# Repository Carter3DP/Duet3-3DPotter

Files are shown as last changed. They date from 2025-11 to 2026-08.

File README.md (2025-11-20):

# Duet3-Mainboard-3DP

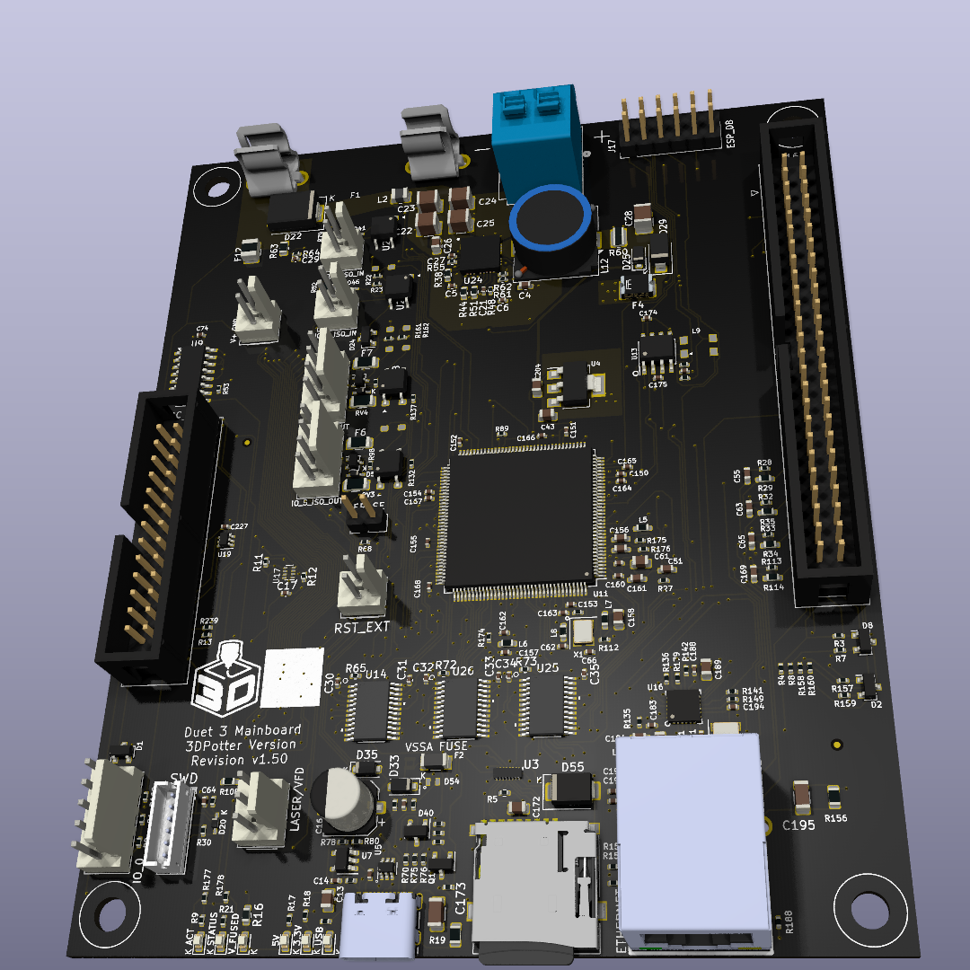
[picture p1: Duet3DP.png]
Render of the board.


This board is a fork of the Duet3 6XD with a little of the 6HC. You can find
them here:

[https://github.com/Duet3D/Duet3-Mainboard-6XD](https://github.com/Duet3D/Duet3-Mainboard-6XD)

[https://github.com/Duet3D/Duet3-Mainboard-6HC](https://github.com/Duet3D/Duet3-Mainboard-6HC)

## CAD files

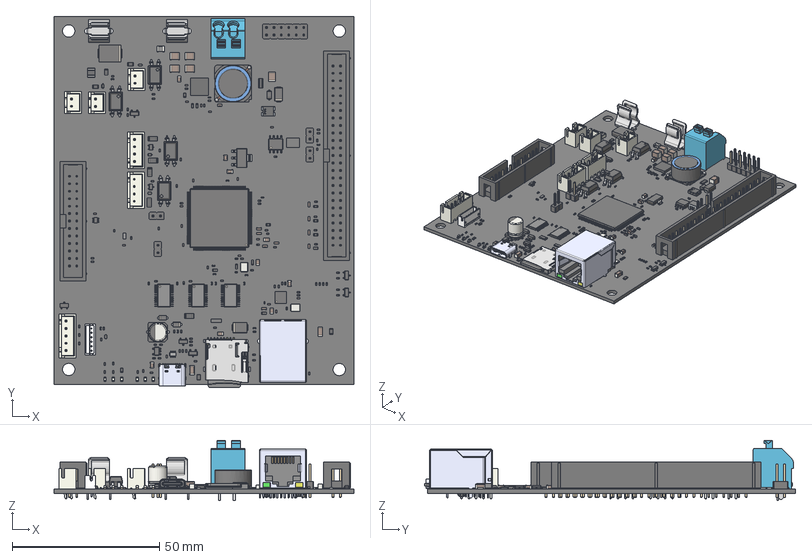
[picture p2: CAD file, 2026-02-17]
CAD/Duet3_MB_3DP.step
101.9 x 126.2 x 20.5 mm
R_0402_1005Metric x 77
SOT-23 x 6
Crystal_SMD_3225-4Pin_3.2x2.5mm x 2
C_0603_1608Metric x 10
BxB-ZR_6
pin_straight x 4
pin_Bent x 2
LED_0603_1608Metric x 6
LQFP-144_20x20mm_P0.5mm
R_0805_2012Metric x 5
R_0603_1608Metric x 13
L_Wurth_WE-CNSW-1812
PinHeader_1x02_P2.54mm_Vertical x 4
D_SOD-523 x 5
C_1206_3216Metric x 2
C_0402_1005Metric x 45
C_0805_2012Metric x 9
SOT-223
Fuse_1206_3216Metric x 3
IDC-Header_2x13_P2.54mm_Vertical
JST_XH_B2B-XH-A_1x02_P2.50mm_Vertical x 3
QFN-24-1EP_4x4mm_P0.5mm_EP2.6x2.6mm
SOIC-8_3.9x4.9mm_P1.27mm
HR911105A_HR911105A
Case^MicroSD_Socket
Insert^MicroSD_Socket
Brace^MicroSD_Socket
Spring^MicroSD_Socket
Lid^MicroSD_Socket
Pin_Middle^MicroSD_Socket x 5
Pin_Short^MicroSD_Socket
Pin_Long^MicroSD_Socket x 2
MicroSD_Card^MicroSD_Socket
Pin_CardIn^MicroSD_Socket
JST_XH_B5B-XH-A_1x05_P2.50mm_Vertical
D_SMB
Fuse_1210_3225Metric
JST_XH_B4B-XH-A_1x04_P2.50mm_Vertical x 2
Pin x 8
SOT-323_SC-70 x 2
R_1206_3216Metric x 2
USB4105GFA_USB4105GFA
L_TDK_SLF12575
PinsArrayLR
CP_Elec_6.3x7.7
PinHeader_2x06_P2.54mm_Vertical
C_1210_3225Metric x 5
BODY-TSSOP x 3
LEAD-TSSOP x 72
PIN1 x 3
R_0612_1632Metric
D_SOD-123F x 3
L_1008_2520Metric
D_SMC
IDC-Header_2x25_P2.54mm_Vertical
D_SMA
MICROQFN16_1P25X3P55X0P4_STM
SOT-23-5
SC70_RCLAMP_SEM
Intersect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

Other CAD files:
CAD/Duet3_MB_6XD.step
CAD/Duet3_MB_3DP (2).step

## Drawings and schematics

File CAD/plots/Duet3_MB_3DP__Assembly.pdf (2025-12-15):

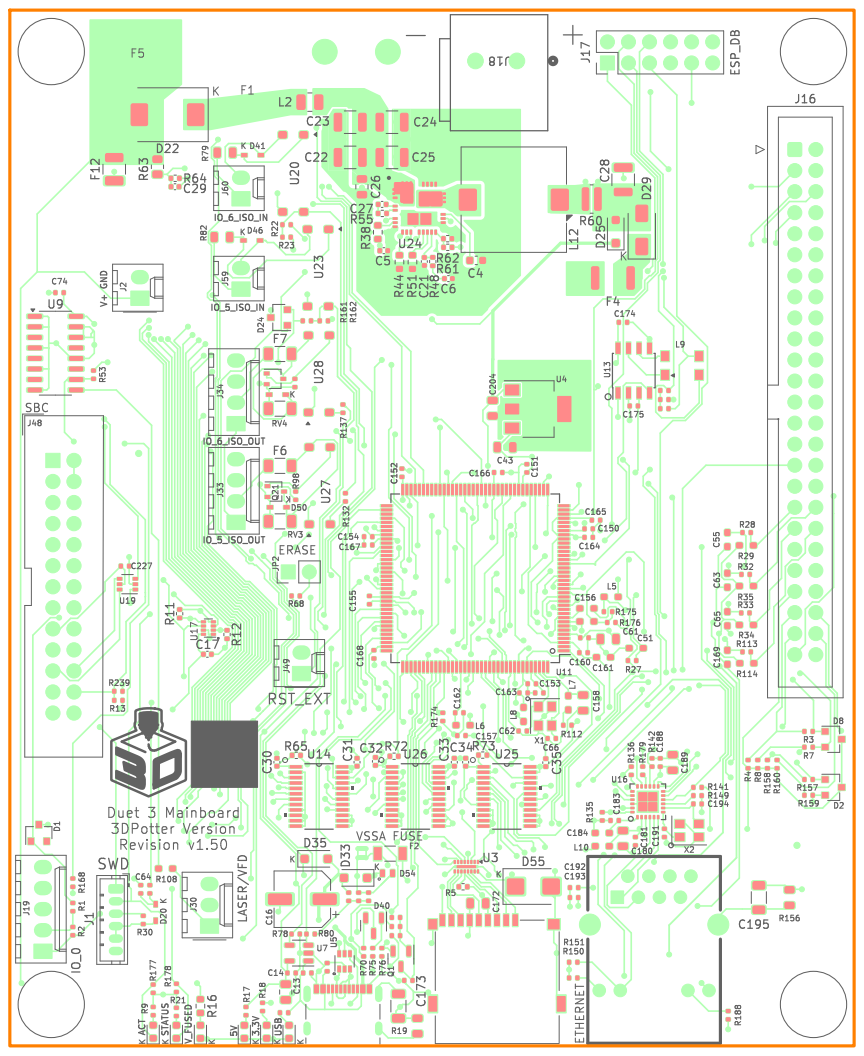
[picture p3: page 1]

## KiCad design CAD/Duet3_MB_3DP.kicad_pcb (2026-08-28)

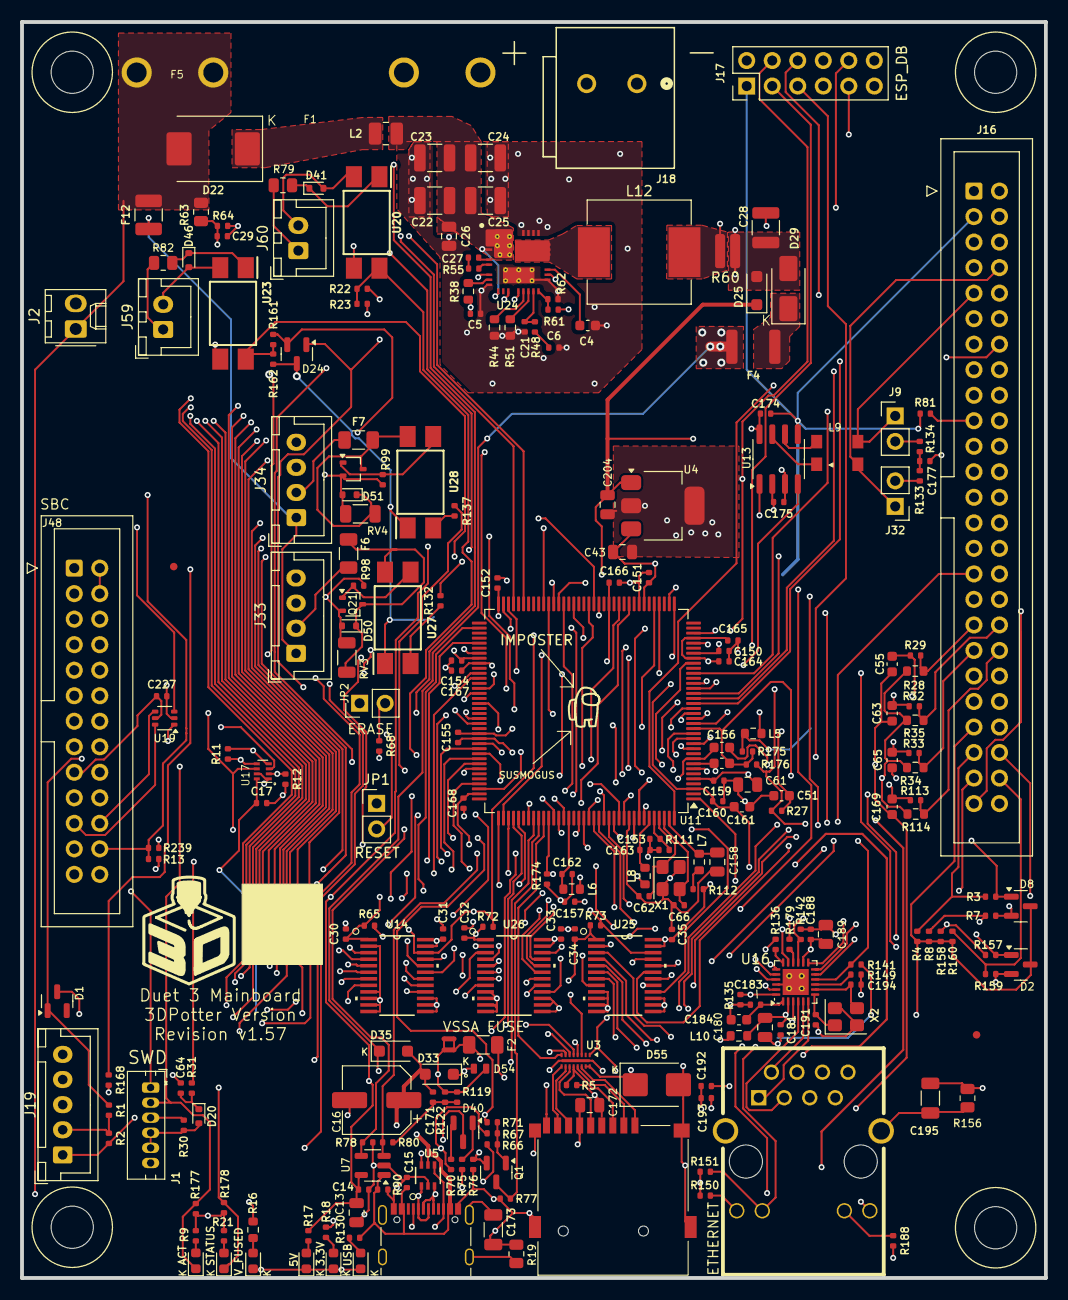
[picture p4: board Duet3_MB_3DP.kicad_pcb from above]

Board: 4 copper layers, 101.9 x 125.0 mm, 253 parts (1 on the bottom side), 214 nets.

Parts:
C4: 2.2uF 10V; C_0603_1608Metric
C5: 470nF 10V; 0402_1005Metric_NoSilk
C6: 15nF 16V; 0402_1005Metric_NoSilk
C13, C43, C172, C180, C189, C204: 10uF 10V; C_0805_2012Metric
C14, C15, C17, C171, C174, C175, C181, C183, C188, C192, C193, C227: 0.1uF 16V; 0402_1005Metric_NoSilk
C16: 100uF 35V; CP_Elec_6.3x7.7
C21: 300pF 25V; 0402_1005Metric_NoSilk
C22, C23, C24, C25: 4.7uF 100V; C_1210_3225Metric
C26: 100nF 100V; C_0805_2012Metric
C27: 47nF 10V; 0402_1005Metric_NoSilk
C28: 47nF 16V; C_1210_3225Metric
C29, C64: 10nF 10V; 0402_1005Metric_NoSilk
C30, C31, C32, C33, C34, C35, C150, C151, C152, C154, C155, C157, C159, C160, C162, C163, C164, C165, C166, C167, C168: 100nF 16V; 0402_1005Metric_NoSilk
C51, C55, C63, C65, C169, C184, C200: 2.2uF 16V; C_0603_1608Metric
C61, C158: 4.7uF 16V; C_0805_2012Metric
C62, C66, C153: 10pF 50V; 0402_1005Metric_NoSilk
C156, C161: 1uF 25V; C_0603_1608Metric
C173, C195: 1nF 1kV; C_1206_3216Metric
C177: 4.7nF 10V; 0402_1005Metric_NoSilk
C191, C194: 22pF 50V; 0402_1005Metric_NoSilk
D1, D2, D8, D24, D40: BAT54C; SOT-23
D4: BLUE; LED_0603_1608Metric
D5, D7, D23: RED; LED_0603_1608Metric
D6, D42: GREEN; LED_0603_1608Metric
D20, D41, D46, D50, D51: 1N4448WT; D_SOD-523
D22: ACDBC5100-HF; D_SMC
D25, D33, D35: 1A,40V; D_SOD-123F
D29: 3A 40V; D_SMA
D54: D_TVS_5V; DFN1610-2L
D55: D_TVS_3.3V; D_SMB
F1, F5: 01220088Z
F2: VSSA FUSE; Fuse_1206_3216Metric
F4: PTC_3A; Fuse_1812_4532Metric
F6, F7: FUSE 60V 50mA/150mA; Fuse_1206_3216Metric
F12: FUSE 90V 300mA-500mA; Fuse_1210_3225Metric
J1: SWD; JST_ZH_B6B-ZR_1x06_P1.50mm_Vertical
J2: A2543WV-2P; Molex_KK-254_AE-6410-02A_1x02_P2.54mm_Vertical
J9, J32: Conn_01x02; PinHeader_1x02_P2.54mm_Vertical
J16: EXPANSION; IDC-Header_2x25_P2.54mm_Vertical
J17: ESP_DB; PinHeader_2x06_P2.54mm_Vertical
J18: 250-502/000-006; CONN2_250-502&slash_000-006_WAG
J19: A2543WV-5P; JST_XH_B5B-XH-A_1x05_P2.50mm_Vertical
J27: uSD_Socket; uSD_SKT
J33, J34: A2543WV-4P; JST_XH_B4B-XH-A_1x04_P2.50mm_Vertical
J43: USB; USB_C_Receptacle_Valcon_CSP-USC16-TR
J46: ETHERNET; RJ45+MAG
J48: SBC; IDC-Header_2x13_P2.54mm_Vertical
J59, J60: A2543WV-2P; JST_XH_B2B-XH-A_1x02_P2.50mm_Vertical
JP1: RESET; PinHeader_1x02_P2.54mm_Vertical
JP2: ERASE; PinHeader_1x02_P2.54mm_Vertical
L2: 1uH; L_1008_2520Metric
L5, L6, L7, L8, L10: 1K @100Mhz; R_0603_1608Metric
L9: CM Choke; LineKey_CM_Choke_SCW_4532A
L12: 10 uH; L_Vishay_IHLP-4040
M1, M2: FID; Fiducial_0.75mm_Mask1.5mm
M3, M9, M11, M15: MOUNTING; Fixing_M4
NT1, NT2: Net-Tie_2; NetTie-2_SMD_Pad0.5mm
Q1: BC807; SOT-23
Q21, Q22: MMBTA06-7-F; SOT-323_SC-70
R1, R3, R7, R18, R22, R27, R29, R30, R32, R33, R77, R80, R113, R142, R151, R157, R159, R161, R174: 10K; 0402_1005Metric_NoSilk
R2, R4, R8, R11, R12, R13, R81, R122, R158, R160: 27K; 0402_1005Metric_NoSilk
R5, R177, R178: 100K; 0402_1005Metric_NoSilk
R9, R21, R76, R136, R141, R239: 1K; 0402_1005Metric_NoSilk
R16: 120K; R_0603_1608Metric
R17, R130: 5K; 0402_1005Metric_NoSilk
R19, R156: 1M; R_0805_2012Metric
R23, R64, R78, R135, R176: 4.7K; 0402_1005Metric_NoSilk
R28, R34, R35, R114: 2.2K 0.1% 0.2W+; R_0603_1608Metric
R31: 180R; 0402_1005Metric_NoSilk
R38: 100k; R_0603_1608Metric
R44: 41.2K; R_0603_1608Metric
R48: 2.61k; 0402_1005Metric_NoSilk
R51: 53.6K; R_0603_1608Metric
R55: 1 Ohm; 0402_1005Metric_NoSilk
R60: 6 mOhm; R_0612_1632Metric
R61: 52.3k; 0402_1005Metric_NoSilk
R62: 10k; 0402_1005Metric_NoSilk
R63: 120K; R_0805_2012Metric
R65, R72, R73, R119: 47K; 0402_1005Metric_NoSilk
R66, R67: 28.7K; 0402_1005Metric_NoSilk
R68, R98, R99: 2.2K; 0402_1005Metric_NoSilk
R70, R75: 2.87K; 0402_1005Metric_NoSilk
R71: 15K; 0402_1005Metric_NoSilk
R79, R82: 10K 0.25W; R_0805_2012Metric
R90, R132, R137, R150, R168, R188: 470R; 0402_1005Metric_NoSilk
R111: 5.62K; 0402_1005Metric_NoSilk
R112: 2.2R; 0402_1005Metric_NoSilk
R133, R134: 59R; 0402_1005Metric_NoSilk
R149: 6.49K; 0402_1005Metric_NoSilk
R162: 4.7k; 0402_1005Metric_NoSilk
R175: 15R; 0402_1005Metric_NoSilk
R179: 27R; 0402_1005Metric_NoSilk
RV3, RV4: VE1206K121R050; R_1206_3216Metric
TM1: 3DPotter Logo 10x10mm
TM2: Amogus
TP39: VREFP; TestPoint_Pad_D1.5mm
U3: EMIF06; QFN-16L-3.5x1.2mm_P0.4mm
U4: AP7361C-33E-13; SOT-223
U5: RClamp0504FB; SC70_RCLAMP_SEM
U7: AP22816AKEWT; SOT-23-5
U11: ATSAME70Q20B-ANT; LQFP-144_20x20mm_P0.5mm
U13: MCP2542; SOIC-8_3.9x4.9mm_P1.27mm
U14, U25, U26: SN74LVC4245APWR; PW24
U16: KSZ8081RNACA; QFN-24-1EP_4x4mm_P0.5mm_EP2.6x2.6mm_THT
U17: 74LVC2G125; X2-DFN2010-8
U19: 74LVC2G34; SOT-363_SC-70-6
U20, U23, U27, U28: Optoisolator; SOP254P1016X460-4N
U24: LM70860RRXR; RRX0029B-MFG
X1: ECS-120-10-33B-CKM-TR; Crystal_SMD_3225-4Pin_3.2x2.5mm
X2: 25Mhz; Crystal_SMD_3225-4Pin_3.2x2.5mm

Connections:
5V_EXT: D35.1 (K), F4.1, J16.1, J19.5
5V_INT: C13.1, C14.1, C30.1, C32.1, C34.1, C175.1, C204.1, D25.1 (K), D33.1 (K), D54.1 (K), R17.1, R65.2, R72.2, R73.2, U4.1 (IN), U7.5 (IN), U13.3 (VDD), U14.1 (VCCA), U25.1 (VCCA), U26.1 (VCCA)
5V_SBC: J48.2, J48.4
+3.3V: C17.1, C31.1, C33.1, C35.1, C43.1, C61.1, C150.1, C151.1, C152.1, C154.1, C155.1, C157.1, C159.1, C172.1, C174.1, D1.3, D2.3, D8.3, D24.3, D55.1 (K), J1.3, J16.3, J16.43, J17.1, J19.1, J27.4 (VDD), JP2.1, L5.1 (A), L10.1 (A), R2.2, R4.2, R5.2, R8.2, R9.1, R13.2, R18.1, R21.1, R23.2, R30.2, R81.2, R112.1, R136.1, R141.1, R150.1, R151.1, R158.2, R160.2, R162.2, R177.2, R178.2, U3.15 (VCC), U3.16 (RDATA_VCC), U4.3 (OUT), U11.5 (VDDIN), U11.30 (VDDIO), U11.43 (VDDIO), U11.72 (VDDIO), U11.80 (VDDIO), U11.96 (VDDIO), U11.134 (VDDUTMII), U13.5 (VIO), U14.23 (VCCB), U14.24 (VCCB), U17.8 (VCC), U25.23 (VCCB), U25.24 (VCCB), U26.23 (VCCB), U26.24 (VCCB), U27.1, U28.1
/Comms/CAN1H_C: L9.1, U13.7 (CANH)
/Comms/CAN1L_C: L9.4, U13.6 (CANL)
/Comms/CLK: J27.5 (CLK), U3.11 (CLK)
/Comms/CMD: J27.3 (CMD), R5.1, U3.12 (CMD)
/Comms/DAT0: J27.7 (DAT0/DO), U3.10 (Data0)
/Comms/DAT1: J27.8 (DAT1), U3.9 (Data1)
/Comms/DAT2: J27.1 (DAT2), U3.14 (Data2)
/Comms/DAT3: J27.2 (DAT3), U3.13 (Data3)
/Comms/LED0: J46.10 (LEDG_K), R151.2, U16.23 (LED0)
/Comms/RD+: J46.3 (RD+), U16.4 (RXP)
/Comms/RD-: J46.6 (RD-), U16.3 (RXM)
/Comms/REF_CLK: R179.2, U16.16 (REF_CLK)
/Comms/REXT: R149.1, U16.9 (REXT)
/Comms/SHIELD_GND: C195.2, J46.8 (GND), J46.13 (SHIELD), J46.14 (SHIELD), R156.2
/Comms/TD+: J46.1 (TD+), U16.6 (TXP)
/Comms/TD-: J46.2 (TD-), U16.5 (TXM)
/Comms/VDDA_3V3: C180.1, C181.1, C188.1, C189.1, L10.2 (B), U16.2 (VDDA_3V3), U16.14 (VDDIO)
/Comms/VDD_1V2: C183.1, C184.1, U16.1 (VDD_1V2)
/Comms/XI: C194.2, U16.8 (XI), X2.3
/Comms/XO: C191.2, U16.7 (XO), X2.1
/Comms/can1_term_c: C177.2, R133.2, R134.1
/Comms/cc1d: D40.2, R70.2
/Comms/cc2d: D40.1, R75.2
/Comms/intrp: R136.2, U16.18 (INTRP)
/Comms/q1b: Q1.1 (B), R66.1, R67.1, R71.2
/Comms/usbce: C173.1, J43.S1 (SHIELD), R19.1
/IO/opt_io5_i_p: D46.1 (K), R82.2, U23.1
/IO/opt_io5_o: D50.1 (K), F6.2, Q21.3 (C), RV3.1, U27.4
/IO/opt_io5_oc: Q21.1 (B), R98.2, U27.3
/IO/opt_io5_pin: R132.1, U27.2
/IO/opt_io6_i_p: D41.1 (K), R79.2, U20.1
/IO/opt_io6_o: D51.1 (K), F7.2, Q22.3 (C), RV4.1, U28.4
/IO/opt_io6_oc: Q22.1 (B), R99.2, U28.3
/IO/opt_io6_pin: R137.1, U28.2
/Power/5V_Common: C28.1, D25.2 (A), D29.2 (A), R60.2, R61.2, U24.6 (BIAS), U24.12 (VOUT)
/Power/5v_ext_fuse: D29.1 (K), F4.2
/Power/C6_1: C6.1, R48.1
/Power/C27_1: C27.1, R55.1
/Power/CAP_VCC: C4.1, U24.19 (VCC)
/Power/CBOOT: C27.2, U24.4 (CBOOT)
/Power/CONFIG: R44.2, U24.13 (CONFIG)
/Power/EXTCOMP: C21.1, R48.2, U24.15 (EXTCOMP)
/Power/FB: R61.1, R62.2, U24.16 (FB)
/Power/ISNS+: L12.2, R60.1, U24.11 (ISNS+)
/Power/L2: D22.1 (K), L2.1 (A)
/Power/PG_SYNCOUT: R38.2, U24.7 (PG_SYNCOUT)
/Power/RT: R51.2, U24.14 (RT)
/Power/SW: L12.1, U24.20 (SW1), U24.21 (SW2), U24.22 (SW3)
/Power/SW4: R55.2, U24.5 (SW4)
/Power/VDDA: C5.1, R38.1, U24.18 (VDDA)
/Power/VIN1: C22.1, C23.1, C24.1, C25.1, C26.1, L2.2 (B), U24.1 (VIN4), U24.2 (VIN5), U24.3 (VIN6), U24.9 (EN_UVLO), U24.27 (VIN1), U24.28 (VIN2), U24.29 (VIN3)
/Processor/IO_0_O: R168.1, U11.53 (PD26)
/Processor/VBG: C153.1, R111.2, U11.140 (VBG)
/Processor/VDDCORE: C160.1, C161.1, C164.1, C165.1, C166.1, C167.1, C168.1, L6.2 (B), L8.2 (B), U11.3 (VDDOUT), U11.29 (VDDCORE), U11.33 (VDDCORE), U11.50 (VDDCORE), U11.81 (VDDCORE), U11.107 (VDDCORE)
/Processor/VDDPLL: C162.1, L6.1 (A), U11.123 (VDDPLL)
/Processor/VDDPLLUSB: C158.1, L7.1 (A), U11.143 (VDDPLLUSB)
/Processor/VDDUTMIC: C163.1, L8.1 (A), U11.139 (VDDUTMIC)
/Processor/XIN: C66.1, U11.142 (PB9), X1.3
/Processor/XOUT: C62.1, U11.141 (PB8), X1.1
/Processor/rst: C64.1, D20.1 (K), R31.2
CAN1_H: J16.8, J32.1, L9.2
CAN1_L: J9.1, J16.9, L9.3
CANRX1: U11.17 (PC12), U13.4 (RXD)
CANTX1: U11.92 (PD12), U13.1 (TXD)
CC1: J43.A5 (CC1), R67.2, R70.1, U5.6
CC2: J43.B5 (CC2), R66.2, R75.1, U5.4
D0_DIR: J16.6, U26.4 (A2)
D0_EN: J16.7, U26.3 (A1)
D1_DIR: J16.11, U26.5 (A3)
D1_EN: J16.12, U26.6 (A4)
D2_DIR: J16.16, U14.7 (A5)
D2_EN: J16.17, U14.8 (A6)
D3_DIR: J16.21, U26.7 (A5)
D3_EN: J16.22, U26.8 (A6)
D4_DIR: J16.26, U14.5 (A3)
D4_EN: J16.27, U14.6 (A4)
D5_DIR: J16.32, U14.3 (A1)
D5_EN: J16.33, U14.4 (A2)
DRIVER_0_DIR: U11.109 (PB5), U26.20 (B2)
DRIVER_0_EN: U11.105 (PB4), U26.21 (B1)
DRIVER_0_STEP: U11.111 (PC18), U25.21 (B1)
DRIVER_1_DIR: U11.101 (PD10), U26.19 (B3)
DRIVER_1_EN: U11.32 (PA21), U26.18 (B4)
DRIVER_1_STEP: U11.100 (PC16), U25.20 (B2)
DRIVER_2_DIR: U11.77 (PA4), U14.17 (B5)
DRIVER_2_EN: U11.48 (PC7), U14.16 (B6)
DRIVER_2_STEP: U11.127 (PC23), U25.19 (B3)
DRIVER_3_DIR: U11.37 (PA22), U26.17 (B5)
DRIVER_3_EN: U11.46 (PA23), U26.16 (B6)
DRIVER_3_STEP: U11.38 (PC1), U25.18 (B4)
DRIVER_4_DIR: U11.40 (PC3), U14.19 (B3)
DRIVER_4_EN: U11.99 (PA1), U14.18 (B4)
DRIVER_4_STEP: U11.41 (PC4), U25.17 (B5)
DRIVER_5_DIR: U11.84 (PD14), U14.21 (B1)
DRIVER_5_EN: U11.74 (PD17), U14.20 (B2)
DRIVER_5_STEP: U11.86 (PC9), U25.16 (B6)
D_0_STEP_gated: J16.5, U25.3 (A1)
D_1_STEP_gated: J16.10, U25.4 (A2)
D_2_STEP_gated: J16.15, U25.5 (A3)
D_3_STEP_gated: J16.20, U25.6 (A4)
D_4_STEP_gated: J16.25, U25.7 (A5)
D_5_STEP_gated: J16.31, U25.8 (A6)
EN_DIR_GATE: R65.1, R72.1, U11.57 (PD23), U14.22 (~OE), U26.22 (~OE)
ERASE: JP2.2, R68.1, U11.87 (PB12)
ESP_DATA_RDY: J17.8, U11.93 (PA2)
ESP_EN: J17.10, U11.97 (PC14), U17.1 (1OE), U17.7 (2OE)
EXT_SPI_CK: J16.18, U11.144 (PB13)
EXT_SPI_CS: J16.19, R81.1, U11.26 (PB2)
EXT_SPI_DI: J16.14, U11.21 (PB0)
EXT_SPI_DO: J16.13, U11.20 (PB1)
GMDC: U11.113 (PD8), U16.11 (MDC)
GMDIO: R141.2, U11.110 (PD9), U16.10 (MDIO)
GND: C4.2, C5.2, C6.2, C13.2, C14.2, C15.2, C16.2, C17.2, C21.2, C22.2, C23.2, C24.2, C25.2, C26.2, C28.2, C29.2, C30.2, C31.2, C32.2, C33.2, C34.2, C35.2, C43.2, C51.2, C61.2, C62.2, C64.2, C66.2, C150.2, C151.2, C152.2, C153.2, C154.2, C155.2, C157.2, C158.2, C159.2, C160.2, C161.2, C162.2, C163.2, C164.2, C165.2, C166.2, C167.2, C168.2, C171.2, C172.2, C173.2, C174.2, C175.2, C177.1, C180.2, C181.2, C183.2, C184.2, C188.2, C189.2, C191.1, C192.2, C193.2, C194.1, C195.1, C204.2, C227.2, D4.1 (K), D5.1 (K), D6.1 (K), D23.1 (K), D54.2 (A), D55.2 (A), J1.6, J2.2, J16.2, J16.30, J16.42, J17.2, J17.12, J18.1, J19.3, J27.6 (GND), J27.G (GND), J33.4, J34.4, J43.A1 (GND), J43.A12 (GND), J43.B1 (GND), J43.B12 (GND), J48.6, J48.9, J48.14, J48.20, J48.25, JP1.1, NT1.2, NT2.2, R11.2, R12.2, R19.2, R44.1, R51.1, R62.1, R64.2, R68.2, R76.2, R77.2, R78.2, R90.2, R111.1, R119.2, R135.2, R142.2, R149.2, R156.1, R174.2, R188.2, U3.PAD (GND), U4.2 (GND), U4.4 (GND), U5.2, U7.2 (GND), U11.44 (GND), U11.61 (GND), U11.95 (GND), U11.115 (GND), U11.135 (GND), U11.138 (GND), U13.2 (VSS), U13.8 (S), U14.2 (DIR), U14.9 (A7), U14.10 (A8), U14.11 (GND), U14.12 (GND), U14.13 (GND), U14.14 (B8), U14.15 (B7), U16.22 (GND1), U16.25 (GND2), U17.4 (GND), U19.2 (GND), U20.3, U23.3, U24.8 (PFM_SYNCIN), U24.17 (AGND), U24.23 (PGND1), U24.24 (PGND2), U24.25 (PGND3), U24.26 (PGND4), U24.30 (PGND), U25.2 (DIR), U25.9 (A7), U25.10 (A8), U25.11 (GND), U25.12 (GND), U25.13 (GND), U25.14 (B8), U25.15 (B7), U26.2 (DIR), U26.9 (A7), U26.10 (A8), U26.11 (GND), U26.12 (GND), U26.13 (GND), U26.14 (B8), U26.15 (B7), X1.2, X1.4, X2.2, X2.4
GRX0: U11.125 (PD5), U16.13 (RXD0)
GRX1: U11.121 (PD6), U16.12 (RXD1)
GRXDV: R142.1, U11.126 (PD4), U16.15 (CRS_RV)
GRXER: R174.1, U11.119 (PD7), U16.17 (RXER)
GTX0: U11.131 (PD2), U16.20 (TXD0)
GTX1: U11.128 (PD3), U16.21 (TXD1)
GTXCK: R179.1, U11.1 (PD0)
GTXEN: U11.132 (PD1), U16.19 (TXEN)
HSDN: J43.A7 (D-), J43.B7 (D-), U5.1, U11.136 (HSDM)
HSDP: J43.A6 (D+), J43.B6 (D+), U5.3, U11.137 (HSDP)
IO_0: D1.1, R1.1, U11.52 (PD25)
IO_0_IN: J19.2, R1.2, R2.1
IO_0_OUT: J19.4, R168.2
IO_1: D8.1, R3.1, U11.106 (PD15)
IO_1_IN: J16.45, R3.2, R4.1
IO_2: D8.2, R7.1, U11.71 (PD28)
IO_2_IN: J16.46, R7.2, R8.1
IO_3: D2.1, R157.1, U11.28 (PE5)
IO_3_IN: J16.47, R157.2, R158.1
IO_4: D2.2, R159.1, U11.34 (PD30)
IO_4_IN: J16.48, R159.2, R160.1
IO_5: D24.2, R161.1, U11.23 (PA19)
IO_5_IN: J16.49, R161.2, R162.1, U23.4
IO_5_IN_ISO_NEG: D46.2 (A), J59.2, U23.2
IO_5_IN_ISO_POS: J59.1, R82.1
IO_5_OUT_ISO: R132.2, U11.63 (PD21)
IO_5_OUT_ISO_NEG: D50.2 (A), J33.3, Q21.2 (E), R98.1, RV3.2
IO_5_OUT_ISO_POS: F6.1, J33.2
IO_6: D24.1, R22.1, U11.24 (PA18)
IO_6_IN: J16.50, R22.2, R23.1, U20.4
IO_6_IN_ISO_NEG: D41.2 (A), J60.2, U20.2
IO_6_IN_ISO_POS: J60.1, R79.1
IO_6_OUT_ISO: R137.2, U11.102 (PA0)
IO_6_OUT_ISO_NEG: D51.2 (A), J34.3, Q22.2 (E), R99.1, RV4.2
IO_6_OUT_ISO_POS: F7.1, J34.2
MCCDA: U3.5 (SDCMD), U11.112 (PA28)
MCCK: U3.6 (SDClk), U11.59 (PA25)
MCDA0: U3.7 (SDData0), U11.116 (PA30)
MCDA1: U3.8 (SDData1), U11.118 (PA31)
MCDA2: U3.3 (SDData2), U11.62 (PA26)
MCDA3: U3.4 (SDData3), U11.70 (PA27)
unnamed: D4.2 (A), R16.2
unnamed: D5.2 (A), R17.2
unnamed: D6.2 (A), R18.2
unnamed: D7.2 (A), R21.2
unnamed: D23.2 (A), R130.2
unnamed: D42.2 (A), R9.2
unnamed: J9.2, R134.2
unnamed: J32.2, R133.1
unnamed: J46.9 (LEDG_A), R150.2
unnamed: J46.11 (LEDY_K), R188.1
unnamed: C193.1, J46.5 (RCT)
unnamed: C192.1, J46.4 (TCT)
unnamed: L7.2 (B), R112.2
PHY_RESET: J46.12 (LEDY_A), R135.1, U11.98 (PD11), U16.24 (~RST)
RESET: D20.2 (A), J1.4, J1.5, R30.1, U11.83 (NRST)
RESET_EXT: J16.44, JP1.2, R31.1
SBC_3.3V: C227.1, J48.17, U19.5 (VCC)
SD_CD: J27.9 (Card_Detect), U3.1 (CD), U11.129 (PA29)
SPI1_CS0: J17.6, J48.24, R13.1, R239.1
SPI1_DATA_RDY: J17.4, U11.7 (PE2), U19.3
SPI1_DATA_RDY_BUFF: J48.22, U19.4
SPI1_MISO: J17.5, U11.13 (PC26), U19.1
SPI1_MISO_BUFF: J48.21, U19.6
SPI1_MOSI: J48.19, R11.1, U17.5 (2A)
SPI1_MOSI_BUFF: J17.3, U11.12 (PC27), U17.3 (2Y)
SPI1_SPCK: J48.23, R12.1, U17.2 (1A)
SPI1_SPCK_BUFF: J17.7, U11.130 (PC24), U17.6 (1Y)
STEP_GATE: R73.1, U11.60 (PD22), U25.22 (~OE)
SWCLK: D42.1 (K), J1.2, R177.1, U11.89 (PB7)
SWDIO: D7.1 (K), J1.1, R178.1, U11.79 (PB6)
TEMP_0: C55.1, R29.2, U11.18 (PC15)
TEMP_1: C63.1, R32.2, U11.16 (PC29)
TEMP_2: C65.1, R33.2, U11.11 (PC0)
TEMP_3: C169.1, R113.2, U11.14 (PC31)
THERMISTOR_0: J16.35, R28.2, R29.1
THERMISTOR_1: J16.36, R32.1, R35.2
THERMISTOR_2: J16.37, R33.1, R34.2
THERMISTOR_3: J16.38, R113.1, R114.2
URXD4: J17.11, U11.69 (PD18)
USB_PWR_EN: R78.1, U7.4 (~EN), U11.54 (PC6)
USB_STATE: D40.3, Q1.2 (E), R71.1, R76.1, U11.120 (PC20)
USB_UFP_DETECT: Q1.3 (C), R77.1, U11.117 (PC19)
UTXD4: J17.9, U11.67 (PD19)
VBUS: C15.1, C16.1, D33.2 (A), D35.2 (A), J43.A4 (VBUS), J43.A9 (VBUS), J43.B4 (VBUS), J43.B9 (VBUS), R90.1, R122.1, R130.1, U5.5, U7.1 (OUT)
VBUS_DETECT: C171.1, R80.1, R119.1, R122.2
VIN_POWER_MON: C29.1, R63.2, R64.1, U11.22 (PA20)
VREFN: C55.2, C63.2, C65.2, C156.2, C169.2, C200.2, F2.2, NT1.1, NT2.1, U11.8 (VREFN)
VREFP: C156.1, L5.2 (B), R175.1, TP39.1, U11.9 (VREFP)
VREF_MON: C200.1, R28.1, R34.1, R35.1, R114.1, R175.2, R176.1, U11.15 (PC30)
VSSA: F2.1, J16.40, R27.1, R176.2
VSSA_MON: C51.1, R27.2, U11.19 (PC13)
V_FUSED: D22.2 (A), F5.1, F12.2, J2.1, R16.1, R63.1
V_FUSED_IO: F12.1, J33.1, J34.1
V_IN: F1.1, J18.2
spi1cs0: R239.2, U11.133 (PC25)
~FLG: R80.2, U7.3 (~FLG), U11.122 (PC21)

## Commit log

2025-06-19 Add Custom Board
    [Comms.kicad_sch, Duet3_MB_6XD.kicad_pcb, Duet3_MB_6XD.kicad_sch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]
2025-07-02 Fix labels
    [Comms.kicad_sch, Duet3_MB_6XD.kicad_pcb, Endstops.kicad_sch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]
2025-07-30 removed old files from the 6XD, other cleanup
    `pinout.txt` is outdated.
    If you need the files from the 6XD, there's a link in `README.txt`.
    I removed the `.kicad_prl` file. It stores things like "which layer is currently visible".
    [Comms.kicad_sch, Duet3_MB_3DP.kicad_pcb, Duet3_MB_3DP.kicad_sch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]
2025-07-30 WIP redoing board for new print
    Removed version resistors.
    Added pull-up on CMD.
    Working on motors, not routed.
    Added local library for custom parts.
    Ran auto-cleanup of traces and vias (supervised).
    [Comms.kicad_sch, Duet3_MB_3DP.kicad_pcb, Duet3_MB_3DP.kicad_sch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]
2025-07-30 motors have been routed
    [Duet3_MB_3DP.kicad_pcb, Duet3_MB_3DP.kicad_sch, Headers.kicad_sch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]
2025-07-30 update processor order info
    [Duet3_MB_3DP.kicad_pcb, Duet3_MB_3DP.kicad_sch, Processor.kicad_sch]
2025-08-01 update led resistors
    [Comms.kicad_sch, Duet3_MB_3DP.kicad_pcb, Power.kicad_sch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]
2025-08-25 Moved Traces and Final Prep before Batch 2
    [Comms.kicad_sch, Duet3_MB_3DP.kicad_pcb, bom.csv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]
2025-08-26 Change/Fix Ferrite Beads
    L6-L8 Changed back to original values, no clue why I changed them in the first place
    [Duet3_MB_3DP.kicad_pcb, Processor.kicad_sch]
2025-08-27 Add Alternative Part
    YI321611G800-6R0T is a valid replacement for UPB321611T-800Y-N (L4)
    [Duet3_MB_3DP.kicad_pcb, Power.kicad_sch]
2025-08-27 Delete CAD/production directory
    Remove production files
    [bom.csv, designators.csv, positions.csv]
2025-08-28 Replace Obsolete Parts
    It appears that taiyo yuden is phasing out all BK1608 series ferrite beads, changing L5-L8 back to GZ1608D102TF for now.
    [Processor.kicad_sch]
2025-08-28 V
    Same change as last commit, forgot to save PCB schematic
    [Duet3_MB_3DP.kicad_pcb]
2025-10-21 TODO: Finish LM5013, find replacement for TS30041
    [Duet3_MB_3DP.kicad_pcb, Duet3_MB_3DP.kicad_sch, Power.kicad_sch]
2025-11-10 Remove 12V Buck Converter
    No need for it, unnecessarily complicates design, plus I dont feel like designing 2 Buck Converter layouts
    [Headers.kicad_sch, Power.kicad_sch]
2025-11-10 Started LM70860
    New 5V 6A (built for 4A) buck dc/dc converter, higher range of input voltage (4.5V-80V), built for 12V-75V according to https://webench.ti.com/power-designer/switching-regulator/customize/3?VinMin=12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
    [Duet3_MB_3DP.kicad_pcb, Power.kicad_sch]
2025-11-11 LM70860 Components layed out
    Still need to connect voltage monitor and make sure all components can handle higher voltage
    [Power.kicad_sch]
2025-11-11 Schematic 90%
    Still need VIN_POWER_MON and the voltage divider for it, I need to ask robert what voltages are input through there
    [Power.kicad_sch]
2025-11-13 LM70860 Schematic: DONE
    Schematic Finished, physical layout next
    [Power.kicad_sch, Processor.kicad_sch]
2025-11-13 PCB Layout Started
    Current sensing, PG_SYNCOUT to VDDA to GND, CBOOT, Feedback are done! Fuse holder is laid out, but now we need a new power terminal, most likely changing to 250-502/000-006 from WAGO.
    [Duet3_MB_3DP.kicad_pcb, Power.kicad_sch]
2025-11-14 New VIN Connector added
    [Duet3_MB_3DP.kicad_pcb, Headers.kicad_sch]
2025-11-14 PCB Done
    As far as I am aware, everything is done, still needs to be run through JLCDFM.
    [Duet3_MB_3DP.kicad_pcb, Headers.kicad_sch, Power.kicad_sch]
2025-11-14 Update Revision
    [Comms.kicad_sch, Duet3_MB_3DP.kicad_pcb, Duet3_MB_3DP.kicad_sch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]
2025-11-14 Final Touches?
    Top Surface ground plane around LM70860 with star via stitching and some changes for ease of manufacturing.
    [Duet3_MB_3DP.kicad_pcb]
2025-11-17 Misc. QOL
    Moved some vias around, added some vias, etc.
    Board passed DFM.
    [Comms.kicad_sch, Duet3_MB_3DP.kicad_pcb, Duet3_MB_3DP.kicad_sch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]
2025-11-17 QOL
    Added a buttload of 3d models, 3d model of board is now usable. Also saved a lot of missing symbols and footprints, which are available in the 3DPotter Library.
    [Comms.kicad_sch, Duet3_MB_3DP.kicad_pcb, Headers.kicad_sch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]
2025-11-17 Started SN74LVC4245APWR
    This chip is a dedicated 3v3-5v converter, 24 mA output
    [Stepper_Drv.kicad_sch]
2025-11-18 Finish SN74LVC4245APWR schematic
    Also adds a new pin to the mcu, "EN_DIR_GATE" serves same function as "STEP_GATE" this is necessary for the SN74LVC to power up safely. Pin is driven low to enable the device.
    [Processor.kicad_sch, Stepper_Drv.kicad_sch]
2025-11-19 12 Unconnected left
    Almost done :) Brian fried
    [Duet3_MB_3DP.kicad_pcb, Stepper_Drv.kicad_sch]
2025-11-19 11 Unconnected
    Took me while to make little progress, all because only now have I realized how bad FreeRouting's pathfinding is. So I redid a lot of the traces, bringing them all along a single path clockwise aroun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
    [Duet3_MB_3DP.kicad_pcb]
2025-11-19 6 Unconnected
    [Duet3_MB_3DP.kicad_pcb]
2025-11-19 Done
    Just needs DFM check then it should be ready to send to JLC
    [Duet3_MB_3DP.kicad_pcb]
2025-11-20 Misc Changes
    [Duet3_MB_3DP.kicad_pcb, Power.kicad_sch, Stepper_Drv.kicad_sch]
2025-11-20 Remove Step gate
    [Duet3_MB_3DP.kicad_pcb, Processor.kicad_sch]
2025-11-20 So much QOL
    The boards design is shit. I wonder whose fault that is?
    [Duet3_MB_3DP.kicad_pcb]
2025-11-21 remove step gate pull down resistor
    change D22 to the correct manufacturer part number
    [Duet3_MB_3DP.kicad_pcb, Power.kicad_sch, Processor.kicad_sch]
2025-11-24 Useless push
    [Duet3_MB_3DP.kicad_sch]
2025-11-27 No physical board changes
    Update a datasheet
    removed a comment (Carter reworked the libraries a while - thanks Carter)
    [Comms.kicad_sch, Duet3_MB_3DP.kicad_sch]
2025-12-09 Misc Resistor changes
    [Comms.kicad_sch, Power.kicad_sch]
2025-12-15 Fix Part Name
    [Headers.kicad_sch]
2025-12-22 Wago confuses me
    [Headers.kicad_sch]
2025-12-29 OOPS, switched the symbols for psoitive and negative
    [Comms.kicad_sch, Duet3_MB_3DP.kicad_pcb]
2026-01-02 Pin Changes / Misc
    Changing some pins around so I have a chip select
    Processor Pins:
    PC28 ---> PA9 (Driver_2_Step)
    PC29[AFE1_AD4] ---> PB1[AFE1_AD0] (TEMP_1)
    PC28 -> spi1cs1
    PC29 -> spi1cs2 (Unused as of now)
    IDC Header:
    CAN 0 Lines removed
    13 -> SPI1_MOSI_BUFF
    14 -> SP1_MISO
    18 -> SPI1_SPCK_BUFF
    19 -> spi1cs1
    Misc:
    Fixed all library links, should get a lot less errors now
    [Comms.kicad_sch, Endstops.kicad_sch, Headers.kicad_sch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]
2026-01-02 WIP PCB layout
    This is gonna take a little time
    [Duet3_MB_3DP.kicad_pcb]
2026-01-06 Board Finished
    Board has been slightly modified to add SPI to the BBC.
    A lot of library mismatch/ not found errors were fixed. Only errors that exist currently are all related to the silkscreen edges on all 0402 components.
    [Comms.kicad_sch, Duet3_MB_3DP.kicad_pcb, Headers.kicad_sch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]
2026-01-19 move driver 2 step to be on the same port as the others
    this is moderately important (not critical, but better for software reasons)
    also I added the silkscreen issues to 'ignore'
    also routed the pin change
    [Duet3_MB_3DP.kicad_pcb, Processor.kicad_sch]
2026-01-19 REVERTED BRANCH
    Files got mega corrupted, I reverted to commit e998203. I made roberts changes in this one, so D2 Step is on PC23.
    [Duet3_MB_3DP.kicad_pcb, Processor.kicad_sch]
2026-02-17 V1.55 Pre Maufacturing
    Final change for 1.55, changed connectors to jst due to board height issues with the stepper boards
    DFM passed
    [Comms.kicad_sch, Duet3_MB_3DP (2).step, Duet3_MB_3DP.kicad_pcb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]
2026-06-02 Update Revision 1.56
    1.56 Should be production board that is going on all scara* and cartesian printers. 1.56 is a final check that everything is silkscreened properly and all connectors are the correct ones.
    *Not all scaras. Only scara that does not have this board should be Jarret Gross' scara
    [Comms.kicad_sch, Duet3_MB_3DP.kicad_pcb, Headers.kicad_sch]
2026-06-11 Finalize changes for 1.56
    LCSC and P/N updated for excessively out of stock parts.
    Silkscreen changes so no more DRC errors
    [Comms.kicad_sch, Duet3_MB_3DP.kicad_pcb, Duet3_MB_3DP.kicad_sch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]
2026-06-11 Forgot to save
    Same changes as last commit, I forgot to save before pushing
    [Headers.kicad_sch, Power.kicad_sch]
